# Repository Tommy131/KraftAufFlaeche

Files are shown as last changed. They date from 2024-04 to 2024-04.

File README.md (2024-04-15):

# Robotik Arduino Sources

> This repository contains the sources for the controller used by team __Kraft auf Fläche__

## Development process

### Tools

- Preferred: `PlatformIO IDE` for vscode

### Code quality assurance

```bash
# Static code analysis
pio check

# run unit tests (for UNO)
pio test -e unotest -v

# runn unit tests (for kieblitz)
pio test -e wemos_d1_mini32

# ci commands
pio ci --board=uno --lib="." --exclude="src/test" .
pio ci --board=megaatmega2560 --lib="." --exclude="src/test" .
pio ci --board=wemos_d1_mini32 --lib="." .
```

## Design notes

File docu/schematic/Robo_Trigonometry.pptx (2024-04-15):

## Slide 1

dist 2

diff

φ

diff = dist2-dist1
φ=atan((Sensor dist)/(diff))
realDist = sin(φ) * dist1

dist 1

realDist

Sens dist

φ

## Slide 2

diff = dist1-dist2
φ=atan((Sensor dist)/(diff))
realDist = sin(φ) * dist1

Sens dist

dist 2

realDist

dist 1

diff

φ

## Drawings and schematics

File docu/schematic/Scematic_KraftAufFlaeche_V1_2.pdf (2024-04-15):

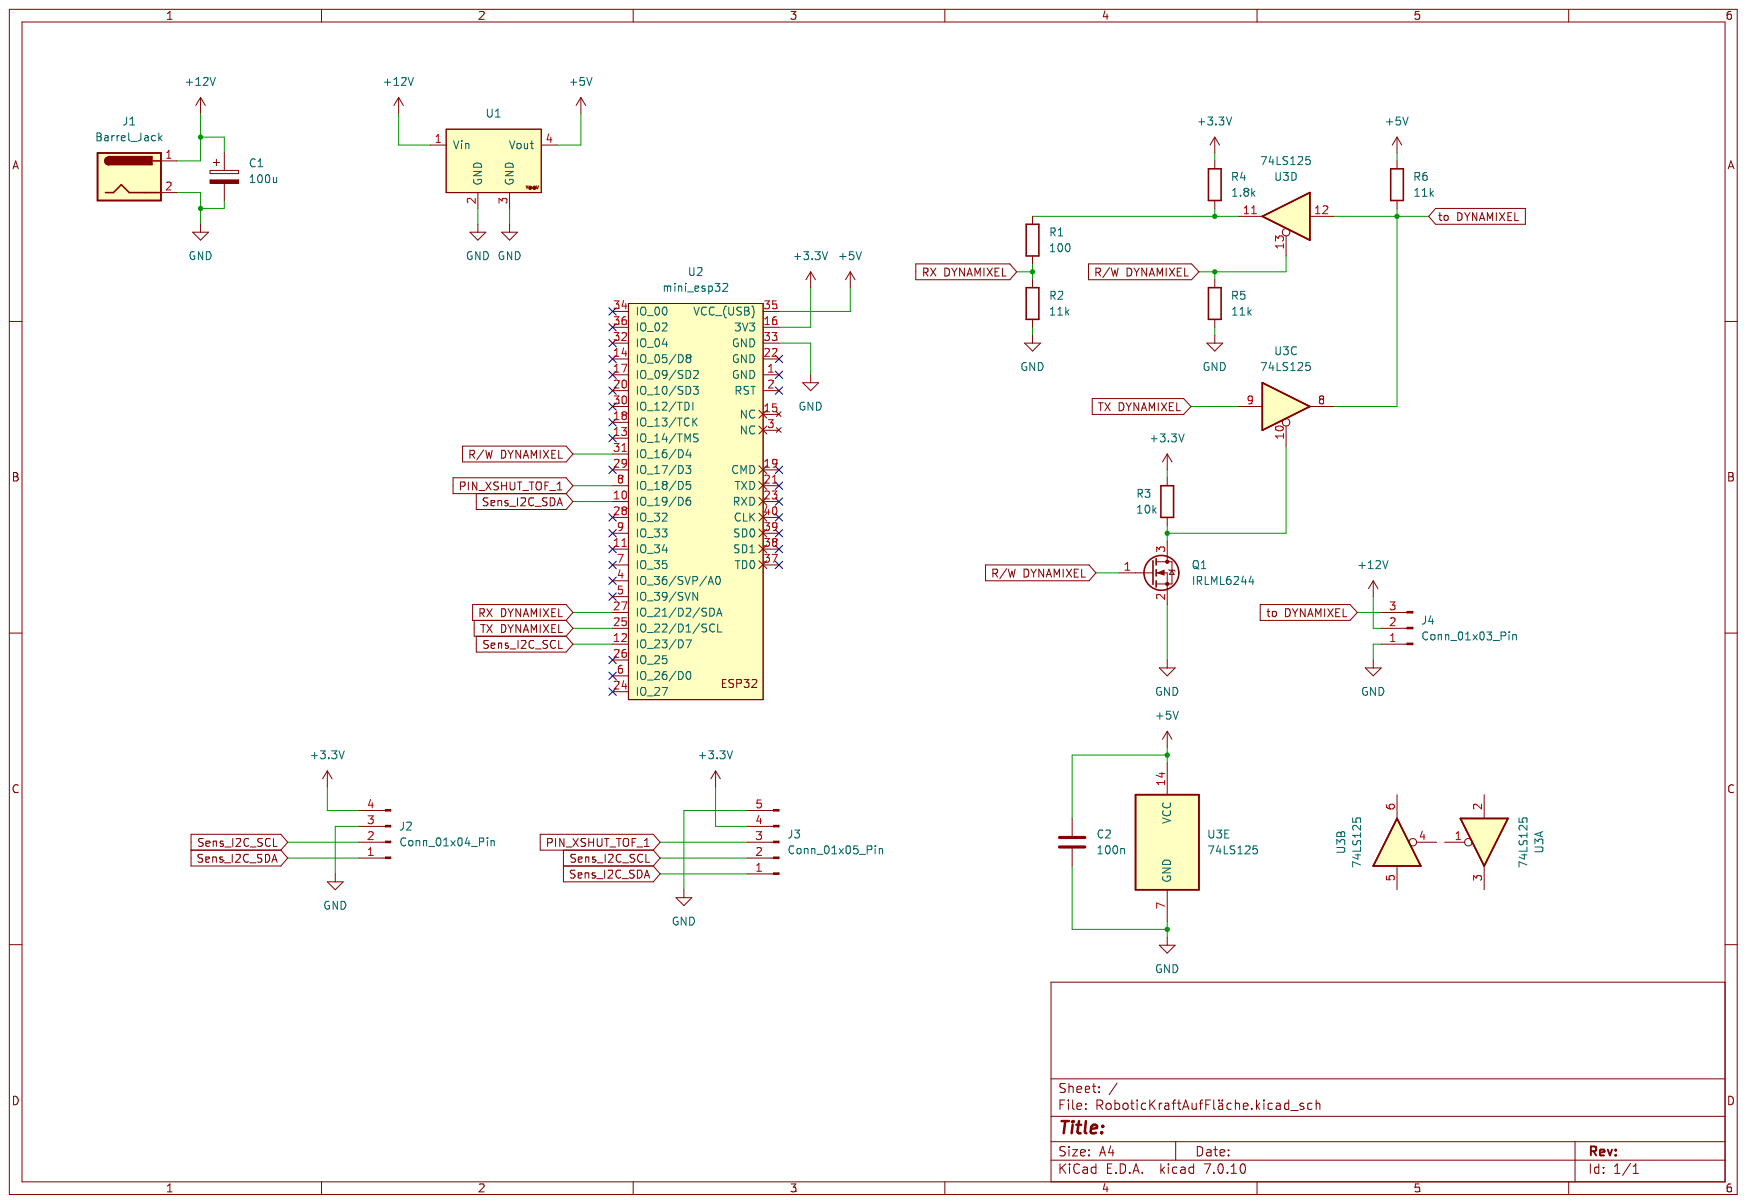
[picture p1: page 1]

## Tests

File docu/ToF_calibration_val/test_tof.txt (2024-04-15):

52,62,82.694241,91,
52,62,82.694241,91,
52,62,82.694241,91,
52,62,82.694241,91,
53,62,83.418057,92,
52,61,83.418057,91,
52,61,83.418057,91,
52,65,80.537677,90,
52,63,81.972761,91,
52,62,82.694241,91,
52,62,82.694241,91,
52,62,82.694241,91,
53,62,83.418057,92,
53,63,82.694241,92,
53,63,82.694241,92,
53,63,82.694241,92,
52,64,81.253836,90,
52,64,81.253836,90,
53,63,82.694241,92,
53,63,82.694241,92,
53,63,82.694241,92,
53,63,82.694241,92,
53,63,82.694241,92,
53,64,81.972761,92,
53,63,82.694241,92,
52,63,81.972761,91,
52,63,81.972761,91,
52,63,81.972761,91,
52,63,81.972761,91,
53,65,81.253836,91,
56,66,82.694241,95,
58,68,82.694241,97,
60,73,80.537677,98,
64,76,81.253836,102,
66,79,80.537677,104,
68,83,79.114470,106,
72,87,79.114470,109,
77,90,80.537677,115,
81,94,80.537677,119,
84,100,78.407826,121,
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

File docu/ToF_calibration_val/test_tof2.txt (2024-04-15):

53,55,88.531198,92,
53,56,87.797403,92,
52,55,87.797403,91,
52,56,87.064326,91,
52,54,88.531198,91,
54,56,88.531198,93,
55,56,89.265477,94,
55,55,90.000003,95,
53,55,88.531198,92,
53,55,88.531198,92,
52,54,88.531198,91,
52,54,88.531198,91,
53,61,84.143990,92,
61,65,87.064326,100,
66,69,87.797403,105,
74,73,89.265477,113,
81,78,87.797403,120,
89,84,86.332211,128,
97,91,85.601292,136,
106,99,84.871808,145,
114,107,84.871808,153,
122,113,83.418057,160,
130,120,82.694241,168,
134,125,83.418057,172,
143,132,81.972761,181,
147,136,81.972761,185,
154,141,80.537677,191,
158,146,81.253836,195,
162,149,80.537677,199,
161,149,81.253836,198,
160,149,81.972761,198,
162,150,81.253836,199,
170,157,80.537677,207,
183,168,79.114470,218,
194,179,79.114470,229,
206,188,77.005383,239,
216,197,76.309947,248,
224,204,75.618602,255,
231,210,74.931512,261,
237,217,75.618602,268,
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

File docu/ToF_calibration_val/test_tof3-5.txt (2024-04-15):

46,46,53,90.000003,86,
46,47,54,89.265477,85,
46,46,53,90.000003,86,
46,47,54,89.265477,85,
46,48,55,88.531198,85,
46,47,54,89.265477,85,
46,45,52,89.265477,85,
47,46,53,89.265477,86,
47,48,55,89.265477,86,
47,47,54,90.000003,87,
48,47,54,89.265477,87,
45,47,54,88.531198,84,
46,49,56,87.797403,85,
46,47,54,89.265477,85,
47,49,56,88.531198,86,
51,49,56,88.531198,90,
50,50,58,90.000003,90,
54,53,61,89.265477,93,
56,57,65,89.265477,95,
60,61,70,89.265477,99,
67,66,76,89.265477,106,
71,71,82,90.000003,111,
77,75,86,88.531198,116,
81,79,90,88.531198,120,
85,82,94,87.797403,124,
89,86,98,87.797403,128,
94,90,103,87.064326,133,
100,96,110,87.064326,139,
104,100,114,87.064326,143,
109,103,118,85.601292,148,
114,107,123,84.871808,153,
119,111,127,84.143990,158,
121,112,128,83.418057,159,
121,113,129,84.143990,160,
121,113,129,84.143990,160,
121,113,129,84.143990,160,
121,113,129,84.143990,160,
120,113,129,84.871808,159,
122,113,129,83.418057,160,
122,114,130,84.143990,161,
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

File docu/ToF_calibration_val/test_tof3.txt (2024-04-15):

72,72,90.000003,112,
72,72,90.000003,112,
72,72,90.000003,112,
73,72,89.265477,112,
73,73,90.000003,113,
72,72,90.000003,112,
72,72,90.000003,112,
73,72,89.265477,112,
72,72,90.000003,112,
72,72,90.000003,112,
72,72,90.000003,112,
73,71,88.531198,112,
74,71,87.797403,113,
73,73,90.000003,113,
73,71,88.531198,112,
73,71,88.531198,112,
73,71,88.531198,112,
72,71,89.265477,111,
72,72,90.000003,112,
72,72,90.000003,112,
72,72,90.000003,112,
72,72,90.000003,112,
72,72,90.000003,112,
72,72,90.000003,112,
72,72,90.000003,112,
72,73,89.265477,111,
73,73,90.000003,113,
73,72,89.265477,112,
73,72,89.265477,112,
73,72,89.265477,112,
73,72,89.265477,112,
73,72,89.265477,112,
72,72,90.000003,112,
73,72,89.265477,112,
73,72,89.265477,112,
72,72,90.000003,112,
72,71,89.265477,111,
71,73,88.531198,110,
71,73,88.531198,110,
71,73,88.531198,110,
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

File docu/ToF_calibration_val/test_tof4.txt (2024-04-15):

43,37,43,85.601292,82,
42,37,43,86.332211,81,
42,37,43,86.332211,81,
43,37,43,85.601292,82,
43,38,44,86.332211,82,
45,38,44,84.871808,84,
44,38,44,85.601292,83,
44,37,43,84.871808,83,
44,37,43,84.871808,83,
44,37,43,84.871808,83,
44,37,43,84.871808,83,
43,37,43,85.601292,82,
41,37,43,87.064326,80,
41,38,44,87.797403,80,
41,37,43,87.064326,80,
43,35,41,84.143990,82,
43,37,43,85.601292,82,
42,37,43,86.332211,81,
44,38,44,85.601292,83,
44,37,43,84.871808,83,
44,37,43,84.871808,83,
44,37,43,84.871808,83,
44,37,43,84.871808,83,
44,37,43,84.871808,83,
44,38,44,85.601292,83,
44,39,45,86.332211,83,
45,41,47,87.064326,84,
45,40,46,86.332211,84,
48,42,48,85.601292,87,
48,45,52,87.797403,87,
52,50,58,88.531198,91,
59,56,64,87.797403,98,
63,58,67,86.332211,102,
67,63,72,87.064326,106,
71,66,76,86.332211,110,
76,71,82,86.332211,115,
82,78,89,87.064326,121,
89,83,95,85.601292,128,
95,88,101,84.871808,134,
101,93,107,84.143990,140,
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

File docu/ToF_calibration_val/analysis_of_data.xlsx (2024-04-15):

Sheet: Test1
 |  |  |  | k | k mean: | 0.8783783784
52 | 62 | 82.694241 | 91 | 0.8387096774
52 | 62 | 82.694241 | 91 | 0.8387096774
52 | 62 | 82.694241 | 91 | 0.8387096774
52 | 62 | 82.694241 | 91 | 0.8387096774
53 | 62 | 83.418057 | 92 | 0.8548387097
52 | 61 | 83.418057 | 91 | 0.8524590164
52 | 61 | 83.418057 | 91 | 0.8524590164
52 | 65 | 80.537677 | 90 | 0.8
52 | 63 | 81.972761 | 91 | 0.8253968254
52 | 62 | 82.694241 | 91 | 0.8387096774
52 | 62 | 82.694241 | 91 | 0.8387096774
52 | 62 | 82.694241 | 91 | 0.8387096774
53 | 62 | 83.418057 | 92 | 0.8548387097
53 | 63 | 82.694241 | 92 | 0.8412698413
53 | 63 | 82.694241 | 92 | 0.8412698413
53 | 63 | 82.694241 | 92 | 0.8412698413
52 | 64 | 81.253836 | 90 | 0.8125
52 | 64 | 81.253836 | 90 | 0.8125
53 | 63 | 82.694241 | 92 | 0.8412698413
53 | 63 | 82.694241 | 92 | 0.8412698413
53 | 63 | 82.694241 | 92 | 0.8412698413
53 | 63 | 82.694241 | 92 | 0.8412698413
53 | 63 | 82.694241 | 92 | 0.8412698413
53 | 64 | 81.972761 | 92 | 0.828125
53 | 63 | 82.694241 | 92 | 0.8412698413
52 | 63 | 81.972761 | 91 | 0.8253968254
52 | 63 | 81.972761 | 91 | 0.8253968254
52 | 63 | 81.972761 | 91 | 0.8253968254
52 | 63 | 81.972761 | 91 | 0.8253968254
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

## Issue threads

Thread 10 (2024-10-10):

Please Make Puplic

SubjectQuit, 2024-10-10:
Hey can you make this Repo public?

Tommy131, 2024-10-11:
All right, I changed the visibility.

________________________________
发件人: SubjectQuit ***@***.***>
发送时间: 2024年10月10日 5:43 下午
收件人: Tommy131/KraftAufFlaeche ***@***.***>
抄送: HanskiJay ***@***.***>; Assign ***@***.***>
主题: [Tommy131/KraftAufFlaeche] Please Make Puplic (Issue #10)

Hey can you make this Repo public?

―
Reply to this email directly, view it on GitHub<https://github.com/Tommy131/KraftAufFlaeche/issues/10>, or unsubscribe<https://github.com/notifications/unsubscribe-auth/AESNHWQBBUGOCEX5LSWU2WDZ22OBBAVCNFSM6AAAAABPXCXH66VHI2DSMVQWIX3LMV43ASLTON2WKOZSGU3TSMRSGQZTSNI>.
You are receiving this because you were assigned.

SubjectQuit, 2024-10-14:
Thank you

Closed 2024-10-14.

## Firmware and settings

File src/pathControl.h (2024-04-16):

#pragma once

#include <Arduino.h>

#if defined(ARDUINO_AVR_UNO) || defined(ARDUINO_AVR_MEGA2560) //Include SoftwareSerial When using Arduino
    #include <SoftwareSerial.h>
#endif

#include "constants.h"
#include "ToF.h"
#include "PID.h"
#include "MotorControl.h"
#include "RuntimeConfig.h"
#include "PidData.h"
#include "IMU.h"


class pathControl {

private:

    enum driveModes{
        drive_normal                = 0,
        drive_corner                = 1,
        drive_corner_2              = 2,
        drive_one_no_new_ToF_data   = 4,
        drive_both_no_new_ToF_data  = 5,
    };

    enum ID_ToFSensor{
        ID_frontTof    = 0,
        ID_backToF     = 1,
    };
    
    SerialType& serial_out;
    
    uint16_t dist; //in mm
    int8_t speed;

    ToF frontToF_default;
    ToF backToF_default;

    ToF *frontToF;
    ToF *backToF;
    
    IMU imu;

    uint32_t lastMS;
    const uint32_t loopIntervalTime = 40; //ms //interval of loop()
    const uint32_t maxTimeCorner = 1000; //ms //max time the robot has to determine if its a corner

    const uint32_t numValidMax = 50; //Loops where the angle has to be valid

    pid::PID pidDefault = pid::PID(default_pid_trim, 0, false, serial_out);
    pid::PID *pidDist;

    pid::PID pidDefaultAngle = pid::PID(default_pid_angle_trim, 0, false, serial_out);
    pid::PID *pidAngle;
    
    MotorControl motorDefault = MotorControl(serial_out);
    MotorControl *motors;

    uint16_t real_ToF_dist;
    float rotation;

    driveModes driveState  = drive_normal;
    float calc_steer = 0;

    size_t numValid = 0;
    float IMUangle;

    float correctAngle(float angle );

    /**
     * @brief checks angle for validity
     * @param angle angle in RAD to be checked
     * @return true if valid, false otherwise
     * */    
    inline bool checkAngle(float angle);

    float getDifference(float num1, float num2);

    #if defined(ARDUINO_ARCH_ESP32)
    TaskHandle_t readI2C;
    static void readI2CTaskImpl( void * parameter);
    void readI2CTask();
    #endif

public:
    pathControl(uint16_t _dist, SerialType& _serial_out, MotorControl *_motors = nullptr, ToF *_front_ToF = nullptr, ToF *_backToF = nullptr, pid::PID *_pidDist = nullptr, pid::PID *_pidAngle = nullptr);
    ~pathControl();

    uint16_t getDist() const        { return dist; }
    void setDist(uint16_t _dist);

    /**
     * @brief startups all uses Objects and sensors
     * @return bool value if init was successful ('true' if successful) 
    */
    bool init();

    /**
     * @brief complete what should be done in one loop with interval defined loopIntervalTime
     * @return outputs output codes defined in enum outputCode (constants.h)
    */
    outputCode loop();

    /**
     * @brief checks ToF sensor for occurrence of a corner in the control surface
     * @param frontORback takes the enum ID_ToFSensor to select the to be evaluated sensor
     * @param checkRotation set to true if the angle should be checked as well
     * @return outputs output codes defined in enum outputCode (constants.h) [OUT_CODE_OK, OUT_CODE_CORNER, OUT_CODE_NO_TOF_MESS]
    */
    outputCode checkForCorner(ID_ToFSensor frontORback, bool checkRotation = true);

    /**
     * @brief executes a shortcut maneuver to shortcut corners 
     * @return outputs output codes defined in enum outputCode (constants.h) [OUT_CODE_OK, OUT_CODE_ERR]
    */
    outputCode shortcutCorner();

    /**
     * @brief set the max. speed for drive
     * @param _speed speed value
    */
    void setSpeed(int8_t _speed);

    /**
     * @brief use both rays of ToF sensors to estimate the current angle the robot has to the wall. 90deg means parallel to the wall.
     * @return returns the angle in RAD 
    */
    float estimateAngle(uint16_t dist1_raw, uint16_t dist2_raw);

    /**
     * @brief use angle and the distance the wall to calculate real distance
     * @return return the distance in mm of perpendicular line
    */
    uint16_t estimateRealDistance(float angle, uint16_t dist_raw);

    /**
     * @brief use estimation functions to calculate the real distance from the wall
     * @return returns distance from wall 
    */
    uint16_t calculateDist(uint16_t dist1_raw, uint16_t dist2_raw);

    /**
     * @brief stops all motors
    */
   void stopMotors();
};

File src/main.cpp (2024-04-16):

#include "pinDef.h"
#include "constants.h"
#include <DynamixelShield.h>
#include "PID.h"
#include "ToF.h"
#include "MotorControl.h"
#include "pathControl.h"
#include "PidData.h"
#include "RuntimeConfig.h"
#include "DummySerial.h"

#if defined(PIO_UNIT_TESTING)
  DummySerial serial_out;
#elif defined(ARDUINO_AVR_UNO) || defined(ARDUINO_AVR_MEGA2560) // When using Arduino
  //Init for SoftSerial
  #include <SoftwareSerial.h>
  SoftwareSerial sw_serial_out(SOFT_DEBUG_RX, SOFT_DEBUG_TX); // DYNAMIXELShield UART RX/TX
  #define serial_out (sw_serial_out)
#elif defined(ARDUINO_ARCH_ESP32)
  #include <DNSServer.h>
  HardwareSerial& serial_out = Serial;
#endif


//Init for PID
pid::PID pidWall(default_pid_trim, 0, false, serial_out);
pid::PID pidAngle(default_pid_angle_trim, 0, false, serial_out);

//Init ToF
ToF backWall(BACK_TOF_VALUE_OFFSET);
ToF frontWall(0);

pathControl path(DEFAULT_DISTANCE, serial_out, nullptr, &frontWall, &backWall, &pidWall, &pidAngle);

#if defined(RUNTIME_CONFIG_ENABLE) && defined(ARDUINO_ARCH_ESP32)
DNSServer dns;
runtimeconfig::RuntimeConfig runtimeConfig(serial_out, dns);
#endif

#ifndef PIO_UNIT_TESTING // for unit testing
void setup() {

  serial_out.begin(BAUD_SERIAL);
  serial_out.println("Setting up...");
  
  pinMode(PIN_XSHUT_TOF_1, OUTPUT);
  digitalWrite(PIN_XSHUT_TOF_1, HIGH);

  #if defined(RUNTIME_CONFIG_ENABLE) && defined(ARDUINO_ARCH_ESP32)
  runtimeConfig.setOnGainDistUpdateCallback([](pid::pid_trim_t& upd) {
    pidWall.setGain(upd);
    pidWall.printGain(upd);
  });

  runtimeConfig.setOnGainAngleUpdateCallback([](pid::pid_trim_t& upd) {
    pidAngle.setGain(upd);
    pidAngle.printGain(upd);
  });


  runtimeConfig.setOnSpeedUpdate([](int8_t speed) {
  path.setSpeed(speed);
  });

  runtimeConfig.setOnDistanceUpdateCallback([](uint16_t distance) {
    path.setDist(distance);
  });

  runtimeConfig.setupRuntimeConfig();
  #endif

#if defined(ARDUINO_ARCH_ESP32)

  serial_out.printf("PathInitCode(1): %d\n", path.init());
  while (touchRead(PIN_TOUCH) >= TOUCH_THR); //Wait for start Signal

#else
  serial_out.print("PathInitCode(1): ");
  serial_out.println(path.init());
#endif

  serial_out.println("Now entering main loop()");
  
} // setup

// uint32_t loop_time = millis();
// uint32_t loop_delta = 0;

void loop() {

  path.loop();
  
  #if defined(RUNTIME_CONFIG_ENABLE) && defined(ARDUINO_ARCH_ESP32)
    runtimeConfig.loopRuntimeConfig();
  #endif

  // serial_out.printf("loopDelta: %dms\n", loop_delta);
  // if(millis()-loop_time > loop_delta) loop_delta = millis()-loop_time;
  // if((millis()%1000) == 0) loop_delta = 0;
  // loop_time = millis();

} // loop
#endif // PIO_UNIT_TESTING


/**
 * Possible Start/Stop config with touch sensor
 * Global:
 *
// bool stopLoop = false;
// uint16_t touchCNT = 0;
 *
 * In loop():
// if(touchRead(PIN_TOUCH) <= TOUCH_THR) touchCNT ++;
// else                                  touchCNT = 0;
// if(touchCNT >= 5000) {
//   stopLoop = !stopLoop;
//   touchCNT = 0;
//   while(touchRead(PIN_TOUCH) <= TOUCH_THR);
// }
// if(!stopLoop){
  path.loop();
// } else {
//   //path.stopMotors();
// }
// runtimeConfig.loopRuntimeConfig();
*/

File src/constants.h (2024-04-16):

#include <Arduino.h>
#include "DummySerial.h"

#pragma once

#define milliTime01 2   //ms  //used for ToF.h
#define BAUD_SERIAL 115200


//pathControl
#define CORNER_THR          300 //mm //If value is bigger or equal a corner is detected
#define MAX_SPEED           40  //% that the controller should aim to meet //TODO increase
#define DEFAULT_DISTANCE    100
#define TURN_ANGLE          80  //DEG //Angle the robot turns at an corner(measured with an IMU)

#define DISTANCE_TOF 78.0 //mm //distance between the two sensors
#define DISTANCE_TOF_MID 40 //mm //distance between rotation point(mid plane of Robot) and sensor
#define BACK_TOF_VALUE_OFFSET -9 //mm //measurement offset of this sensor  
#define ANGLE_TO_WALL_PARALLEL (90 * DEG_TO_RAD) //RAD //angle the robot has if it is parallel to the wall
#define DIFF_ANGLE (30 * DEG_TO_RAD) // RAD //difference angle after witch the angle should be considered not valid (± to ANGLE_TO_WALL_PARALLEL)
#define MAX_ANGLE (ANGLE_TO_WALL_PARALLEL + DIFF_ANGLE) //RAD //if the angle is bigger than the measurement is not valid  
#define MIN_ANGLE (ANGLE_TO_WALL_PARALLEL - DIFF_ANGLE) //RAD //if the angle is smaller than the measurement is not valid  

#ifndef DEG_TO_RAD
    #define DEG_TO_RAD     = (PI/180);
#endif //DEG_TO_RAD
#ifndef RAD_TO_DEG
    #define RAD_TO_DEG     = (1/(PI/180));
#endif //RAD_TO_DEG


//motorControl
#define MAX_PERCENT 100         //%
#define RES_MOTOR_BIT 10        
#define RES_MOTOR (1023)   //bit //resolution of motors

//output codes
enum outputCode{
    OUT_CODE_ERR           = 0,
    OUT_CODE_OK            = 1,   
    OUT_CODE_CORNER        = 2,   //If a corner is detected
    OUT_CODE_NO_TOF_MESS   = 3,   //If no ToF measurement could be done 
    OUT_CODE_ERR_MOTOR     = 4,   //When problems motors are 
    OUT_CODE_INVAL_NUM     = 5,   //If the number Provided is invalid 
    OUT_CODE_PASS          = 6,   //If no ERR or OK state could be determent 
    OUT_CODE_MPU_ERR       = 7,   //If an error with the mpu is present  
};
    

#define PIN_XSHUT_TOF_1 18 //Pin for the Xshut pin of one of the ToF sensors
#define ADDRESS_TOF_1 0x29 //Default Address of second ToF chip
#define ADDRESS_TOF_2 0x60 //Changed Address of second ToF chip

#if defined(ARDUINO_AVR_UNO) || defined(ARDUINO_AVR_MEGA2560) // When using Arduino
    #define SOFT_DEBUG_RX 9
    #define SOFT_DEBUG_TX 10

#elif defined(ARDUINO_ARCH_ESP32)
    #define PIN_TX_DXL 22   // Pin for Tx communication to the Dynamixel
    #define PIN_RX_DXL 21   // Pin for Rx communication to the Dynamixel
    #define PIN_SW_DXL 16   // Pin for the switching between TX/RX
                            // communication to the Dynamixel (DXL)
                            // HIGH -> send to DXL
                            // LOW  -> receive from DXL

    #define PIN_I2C_SDA 19  // Pin for SDA communication to the sensor(s)
    #define PIN_I2C_SCL 23  // Pin for SCL communication to the sensor(s)

    #define PIN_TOUCH   27  // Pin for Capacitive Sensor
    #define TOUCH_THR   60  //Threshold for the Capacitive Pin of ESP32

#endif

#if defined(PIO_UNIT_TESTING)
    typedef DummySerial SerialType;
#elif defined(ARDUINO_AVR_UNO) || defined(ARDUINO_AVR_MEGA2560) // When using Arduino
    #include <SoftwareSerial.h>
    typedef SoftwareSerial SerialType;
#elif defined(ARDUINO_ARCH_ESP32)
    typedef HardwareSerial SerialType;
    #define DXL_SERIAL Serial1
#endif

// #define RUNTIME_CONFIG_ENABLE 1

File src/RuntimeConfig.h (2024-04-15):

#pragma once

#include "constants.h"

#if defined(RUNTIME_CONFIG_ENABLE) && defined(ARDUINO_ARCH_ESP32)

#include <FS.h>
#include <SPIFFS.h>
#include <ESPmDNS.h>
#include <WiFi.h>
#include <AsyncTCP.h>
#include <ESPAsyncWebServer.h>
#include <SPIFFSEditor.h>
#include <Preferences.h>
#include <ArduinoJson.h>
#include <DNSServer.h>

#include "PidData.h"

#define SSID "kraftaufflaeche"
#define PSK "fosbosprojekt"
#define HOSTNAME "esp32"

#define KEY_KP_PID_DIST "KP_PID_DIST"
#define KEY_KI_PID_DIST "KI_PID_DIST"
#define KEY_KD_PID_DIST "KD_PID_DIST"

#define KEY_KP_PID_ANGLE "KP_PID_ANGLE"
#define KEY_KI_PID_ANGLE "KI_PID_ANGLE"
#define KEY_KD_PID_ANGLE "KD_PID_ANGLE"

#define KEY_DISTANCE "DISTANCE"
#define KEY_SPEED "SPEED"

#define PREF_RW_MODE false
#define PREF_RO_MODE true
#define PREF_DOMAIN "TRIM"
#define PREF_INITIALIZED "PREF_INITI"

#define MAX_PREF_LEN 15

namespace runtimeconfig {

template <typename T>
struct persist_pair {
    char key[MAX_PREF_LEN+1]; // max length is 15 (by library)
    T& value;
};

class RuntimeConfig {

public:
    RuntimeConfig(SerialType& _debug_serial, DNSServer& dns);

    void setupRuntimeConfig();
    void loopRuntimeConfig();
    void setOnGainDistUpdateCallback(std::function<void(pid::pid_trim_t& updated)> onTrimUpdate);
    void setOnGainAngleUpdateCallback(std::function<void(pid::pid_trim_t& updated)> onTrimAngleUpdate);
    void setOnDistanceUpdateCallback(std::function<void(uint16_t distance)> _onDistanceUpdate);
    void setOnSpeedUpdate(std::function<void(int8_t speed)> _onSpeedUpdate);
private:
    SerialType& debug_serial;

    std::function<void(pid::pid_trim_t& updated)> onTrimUpdate = [](pid::pid_trim_t& u){};
    std::function<void(pid::pid_trim_t& updated)> onTrimAngleUpdate = [](pid::pid_trim_t& u){};
    std::function<void(uint16_t distance)> onDistanceUpdate = [](uint16_t distance){};
    std::function<void(int8_t speed)> onSpeedUpdate = [](int8_t  speed){};


    // int8_t
    std::function<size_t(const char* name, int8_t val)> putInt8 = [&](const char* name, int8_t val) { return preferences.putChar(name, val); };
    std::function<int8_t(const char* name)> getInt8 = [&](const char* name) { return preferences.getChar(name); };

    // uint16_t
    std::function<size_t(const char* name, uint16_t val)> putUint16 = [&](const char* name, uint16_t val) { return preferences.putUShort(name, val); };
    std::function<uint16_t(const char* name)> getUint16 = [&](const char* name) { return preferences.getUShort(name); };

    // float
    std::function<size_t(const char* name, float val)> putFloat = [&](const char* name, float val) { return preferences.putFloat(name, val); };
    std::function<float(const char* name)> getFloat = [&](const char* name) { return preferences.getFloat(name); };

    // generic
    std::function<bool(const char* name)> testValue = [&](const char* name) { return preferences.isKey(name); };


    std::vector<persist_pair<int8_t>> settingsInt8 {
        (persist_pair<int8_t>) { KEY_SPEED, speed },
    };

    std::vector<persist_pair<uint16_t>> settingsUint16 {
        (persist_pair<uint16_t>) { KEY_DISTANCE, distance },
    };

    std::vector<persist_pair<float>> settingsFloat {
        (persist_pair<float>) { KEY_KP_PID_DIST, currentGainDist.kp },
        (persist_pair<float>) { KEY_KI_PID_DIST, currentGainDist.ki },
        (persist_pair<float>) { KEY_KD_PID_DIST, currentGainDist.kd },

        (persist_pair<float>) { KEY_KP_PID_ANGLE, currentGainAngle.kp },
        (persist_pair<float>) { KEY_KI_PID_ANGLE, currentGainAngle.ki },
        (persist_pair<float>) { KEY_KD_PID_ANGLE, currentGainAngle.kd },
    };


    template <typename T>
    bool check_pairs(Preferences& prefs, std::vector<persist_pair<T>>& pairs);

    template <typename T>
    void writeValues(
        Preferences& prefs,
        std::vector<persist_pair<T>>& pairs,
        std::function<size_t(const char* name, T val)> valSetter);

    template <typename T>
    void readValues(
        Preferences& prefs,
        std::vector<persist_pair<T>>& pairs,
        std::function<T(const char* name)> valGetter);

    template <typename T>
    void addJsonKV(JsonDocument& data, std::vector<persist_pair<T>>& pairs);

    template <typename T>
    void handleIntParam(AsyncWebServerRequest *request, std::vector<persist_pair<T>>& pairs);

    void update_persisted_prefs(Preferences& prefs, pid::pid_trim_t& trim);
    bool read_persisted_prefs(Preferences& prefs);
    void init_persisted_prefs(Preferences& prefs);


    pid::pid_trim_t currentGainDist;
    pid::pid_trim_t currentGainAngle;
    int8_t speed = MAX_SPEED;
    uint16_t distance = DEFAULT_DISTANCE;

    Preferences preferences;
    AsyncWebServer server;
    DNSServer& dnsServer;

};

} // runtimeconfig

#endif

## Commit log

2024-01-21 added PID lib
2024-01-22 fixed bugs in ToF, updated PID and incorporated code review critic
    [MotorControl.cpp, MotorControl.h, ToF.cpp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]
2024-01-22 added Documentation for ToF sensor and powerPoint for "Mitteltreffen"
2024-01-23 adds printf's, put debug RX/TX into constants.h
2024-01-23 replace magic soft serial values
    [main.cpp]
2024-03-16 clangtidy in class MotorControll
2024-03-20 add crude esp32 support
2024-03-20 Fixed many bugs - ToF Tested
    [ToF.cpp, constants.h, main.cpp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]
2024-03-23 adds fix to pin definition description
    [constants.h]
2024-03-23 fix serial for AVR platform
    [main.cpp]
2024-03-23 adds ifdef for ESP32 specific setting on DXL serial
2024-03-23 set ESP32 board as default env
2024-03-28 patch pathControl class with missing functions [Untested]
    [constants.h, pathControl.cpp, pathControl.h]
2024-03-28 added link to used motors
2024-03-30 FIX constructor for pathControl
    [pathControl.cpp]
2024-03-30 Added schematic of PCB
    [RoboticKraftAufFläche.kicad_sch]
2024-03-31 update PID
2024-04-09 add calculation and TOF fix
    [MotorControl.h, ToF.cpp, constants.h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]
2024-04-09 RuntimeConfig: fix types, fixes speed to int8_t
    [RuntimeConfig.cpp, RuntimeConfig.h, main.cpp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]
2024-04-09 cleanup dir
    [RoboticKraftAufFläche.kicad_sch]
2024-04-10 adds github actions CI files and fix printf
    [main.cpp]
2024-04-12 fix CI: adds DummySerial class for tests
    [constants.h, main.cpp, motorcontrol.cpp]
2024-04-12 CI: fix by building test function only on unit testing
    [motorcontrol.cpp]
2024-04-13 adds serial to PID
2024-04-13 ToF fixed and tested calibration
    [analysis_of_data.xlsx]
2024-04-13 runtimeConfig: added second PID
2024-04-13 begin PID tuning around angle
    # - add support for touch to start
    # - speed up ToF measurement time
    # - cleanup main.cpp
2024-04-13 fix CI: add ifdef and change order
    [main.cpp, pathControl.cpp, pathControl.h]
2024-04-14 pathControl: replace magic number
    [constants.h, pathControl.cpp, pathControl.h]
2024-04-14 fix CI: added ifdef
    [pathControl.cpp]
2024-04-14 ADD IMU support
2024-04-15 Added PowerPoint for Presentation
2024-04-15 Fix IMU
2024-04-15 WORKING Corner drive.
    - Increased corner detection time
    - created async read of I2C devices with tasks on ESP32
    - checked loop time
    - new shortcutCorner algorithm
    [constants.h, main.cpp, pathControl.cpp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]
2024-04-16 Fix I2C read error
    [pathControl.cpp, pathControl.h]
2024-04-16 fix i2cRead error
2024-04-16 fix whitespace and comments
    [IMU.cpp, MotorControl.cpp, ToF.cpp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]
